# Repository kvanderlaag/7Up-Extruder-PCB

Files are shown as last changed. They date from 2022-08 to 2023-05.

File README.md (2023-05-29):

# 7-Up Amateur Extruder PCB

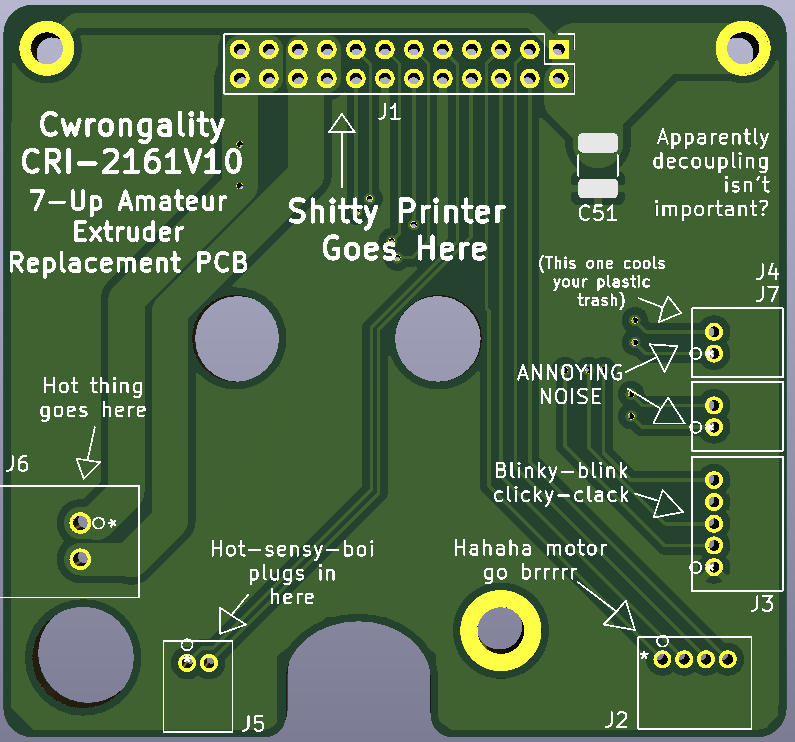
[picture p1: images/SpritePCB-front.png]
Rendering of the front side of a printed circuit board with witty silkscreen text.
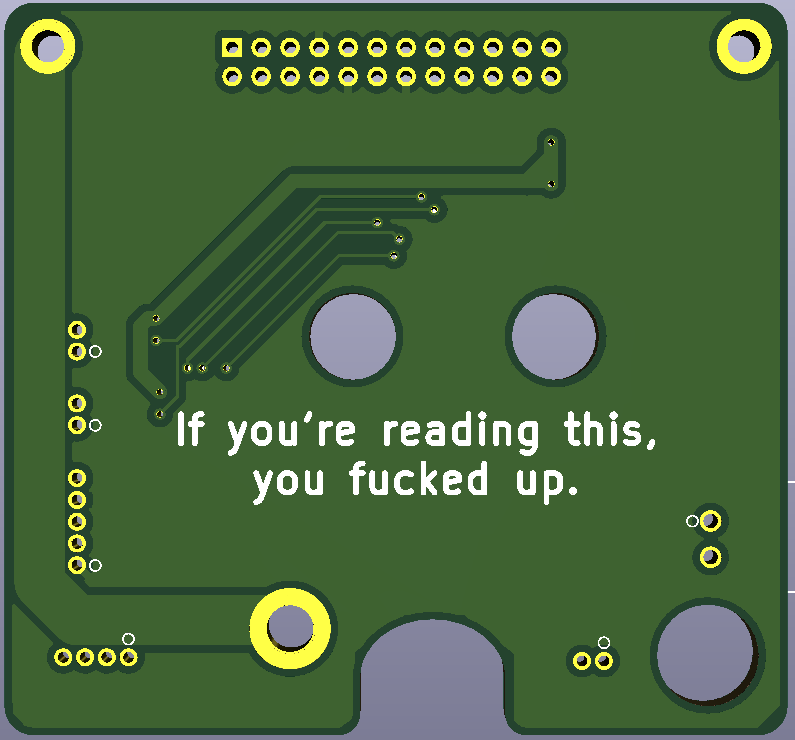
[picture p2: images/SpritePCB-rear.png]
Rendering of the rear side of a printed circuit board with witty silkscreen text.
 

This is a replacement extruder/toolhead PCB for Creality Sprite/Sprite Pro Extruder PCB for Ender-3 series printers -- the Ender-3 S1, Ender-3 S1 Pro, Ender-3 S1 Plus, which all come with a Sprite direct drive extruder out of the box, or an Ender-3, Ender-3 Pro, or Ender-3 V2 that you've retrofitted with the Creality Sprite or Sprite Pro extruder kit.

While fumbling around behind my toolhead with a wrench to adjust the eccentric nut spacer on the X-axis, I managed to ram the wrench into the extruder connector, tearing it off the PCB and taking the solder pads and an appreciable amount of the traces connected to it with it. Naturally, I did this at the worst possible time, when I was printing parts necessary to get my _other_ printer working.

Of note: If you e-mail sales@creality3dofficial.com and request a replacement for this part, they can sell you one! It cost $15 USD shipped. However, while I was waiting to hear back from them, I looked at this PCB and thought, "hell, I could just make one of these."

The connectors on the Creality PCB are: 
- a 2.0mm-pitch, 24-position IDC header, right angle, with locking tabs and eject levers -- they need to be long enough to reach the top of the IDC connector -- for the flat flexible ribbon cable that connects to the printer; ryanpie86 has correctly pointed out that [this connector](https://www.lcsc.com/product-detail/IDC-Connectors_Ckmtw-Shenzhen-Cankemeng-B-3102R24P-A000_C383593.html) on LCSC is a perfect fit, but watch out for LCSC's shipping. It's helpful if you can place an order for a lot of crap together, and you will pay customs fees on it.
- three JST ZH (1.5mm pitch) surface-mount connectors, 2-position, for the thermistor, hotend fan, and part cooling fan
- one JST ZH (1.5mm pitch) surface-mount connector, 4-position, for the extruder motor
- one JST ZH (1.5mm pitch) surface-mount connector, 5-position, for the (optional) CRtouch/BLtouch automatic bed levelling sensor
- one JST XH (2.5mm pitch) through-hole connector, 2-position, for the heater cartridge

I don't know if you've ever soldered these ZH bastards surface-mount before, but they are absolutely hateful little things, and I refuse to do it. ZH is the smallest JST connector size you can get in through-hole flavour, so for this board, I've replaced _all_ of the surface-mount connectors with through-hole variants. I feel like this actually makes this PCB more repairable than the original, and less prone to the thing that destroyed mine in the first place.

The flat flexible cable connector is slightly more problematic. [This](https://www.digikey.ca/en/products/detail/cnc-tech/3110-24-002-13-00/3882488) connector from CnC Tech is exactly what you want -- but it is obsolete and, as far as I can tell, impossible to obtain. Creality are clearly using a connector _like_ this one in the production PCBs, but I haven't been able to find a source for it. If you do, let me know and I'll update the project and this document to point at it. For the time being, I've just carefully desoldered mine from the board and reused it. If you were desperate, you could use a regular shrouded 24-position, 2.0mm pitch, right-angle pin header, but since this part is in motion and dragging the cable around with it, this seems like it probably leads to sadness.

JST connectors are easier to come by, but at the time of this writing (2022-08-25) are spotty at best for stock, with a long lead time. You want the JST [S2B-ZR-3.4(LF)(SN)](https://www.digikey.ca/en/products/detail/jst-sales-america-inc/s2b-zr-3-4-lf-sn/4806278) for the 2-position ZH, [S4B-ZR-3.4(LF)(SN)](https://www.digikey.ca/en/products/detail/jst-sales-america-inc/s4b-zr-3-4-lf-sn/7802286) for the 4-position ZH, [S5B-ZR-3.4(LF)(SN)](https://www.digikey.ca/en/products/detail/jst-sales-america-inc/s5b-zr-3-4-lf-sn/9972250) for the 5-position ZH, and the [S2B-XH-A(LF)(SN)](https://www.digikey.ca/en/products/detail/jst-sales-america-inc/S2B-XH-A-LF-SN/1651055) for the 2-position XH for the heater.

Annoyingly, Chinese replacements available on Alibaba/AliExpress _will_ fit with some massaging, but they are listed at 2.54mm pitch rather than the 2.5mm pitch of "genuine" JSTs. I've designed the board with the JSTs in mind, but there is a distinct probability that the heater cartridge on the Sprite is actually 2.54mm pitch. Again, it should both fit and work whichever one you choose to use, it might just be a little tight on the board if you're using a Chinese XH-style connector, and a little tight fitting the cable into the connector if you're using a genuine JST. The worst of both worlds, really.

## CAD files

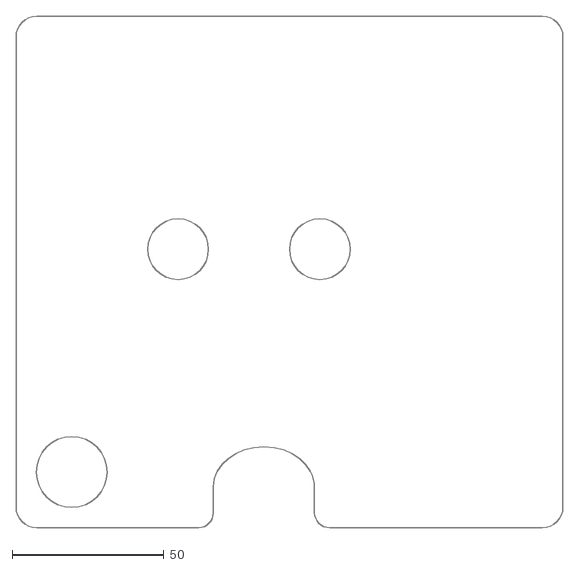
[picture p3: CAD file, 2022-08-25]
Sprite.dxf
180.0 x 168.3

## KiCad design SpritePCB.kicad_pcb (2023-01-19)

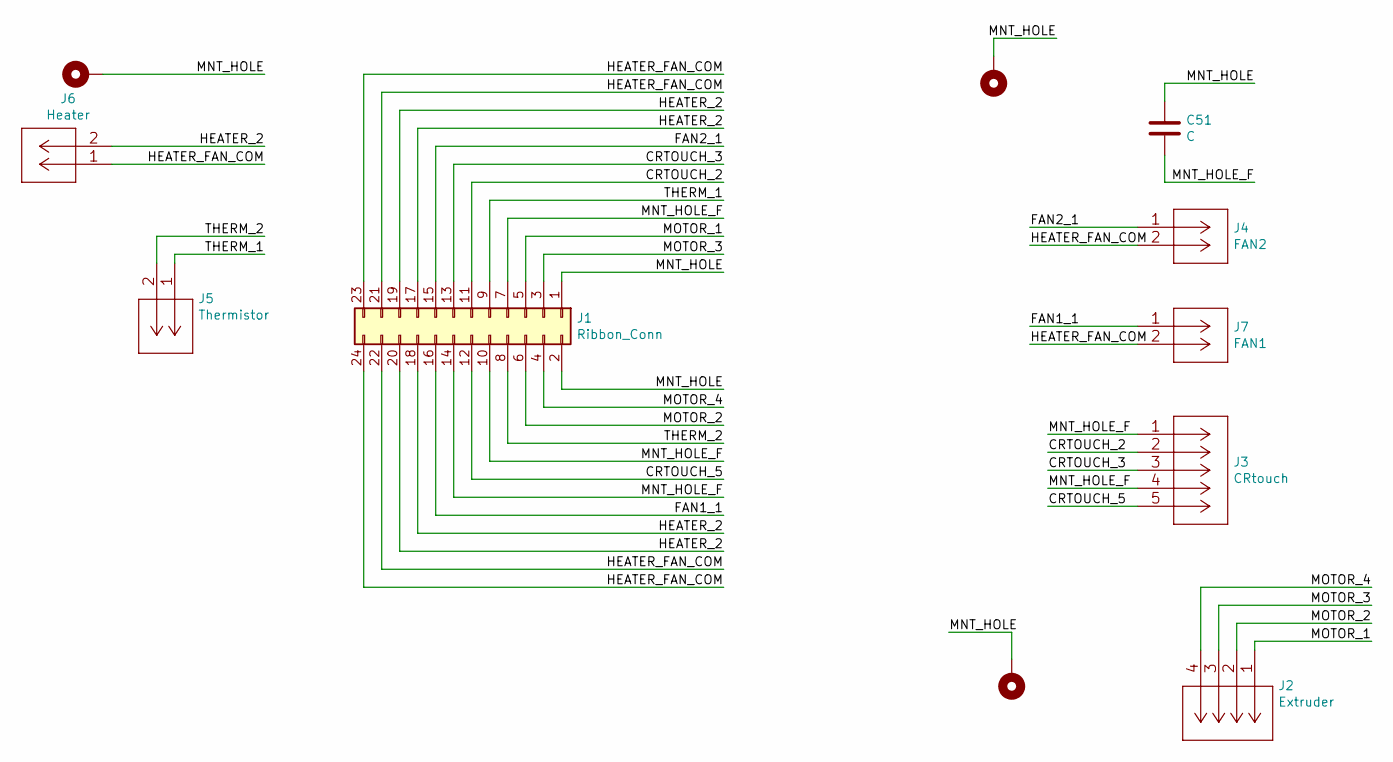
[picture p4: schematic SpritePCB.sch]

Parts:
C51: C; C_1210_3225Metric_Pad1.33x2.70mm_HandSolder
H1, H2: MountingHole_Pad; MountingHole_2.2mm_M2_DIN965_Pad
H3: MountingHole_Pad; MountingHole_3.2mm_M3_DIN965_Pad
J1: Ribbon_Conn; PinHeader_2x12_P2.00mm_Vertical
J2: Extruder; S4B-ZRLFSN
J3: CRtouch; S5B-ZRLFSN
J4: FAN2; S2B-ZRLFSN
J5: Thermistor; S2B-ZRLFSN
J6: Heater; S2B-XH-A-1LFSN
J7: FAN1; S2B-ZRLFSN

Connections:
/CRTOUCH_2: J1.11, J3.2
/CRTOUCH_3: J1.13, J3.3
/CRTOUCH_5: J1.12, J3.5
/FAN1_1: J1.16, J7.1
/FAN2_1: J1.15, J4.1
/HEATER_2: J1.17, J1.18, J1.19, J1.20, J6.2
/HEATER_FAN_COM: J1.21, J1.22, J1.23, J1.24, J4.2, J6.1, J7.2
/MNT_HOLE: C51.1, H1.1, H2.1, H3.1, J1.1, J1.2
/MNT_HOLE_F: C51.2, J1.7, J1.10, J1.14, J3.1, J3.4
/MOTOR_1: J1.5, J2.1
/MOTOR_2: J1.6, J2.2
/MOTOR_3: J1.3, J2.3
/MOTOR_4: J1.4, J2.4
/THERM_1: J1.9, J5.1
/THERM_2: J1.8, J5.2

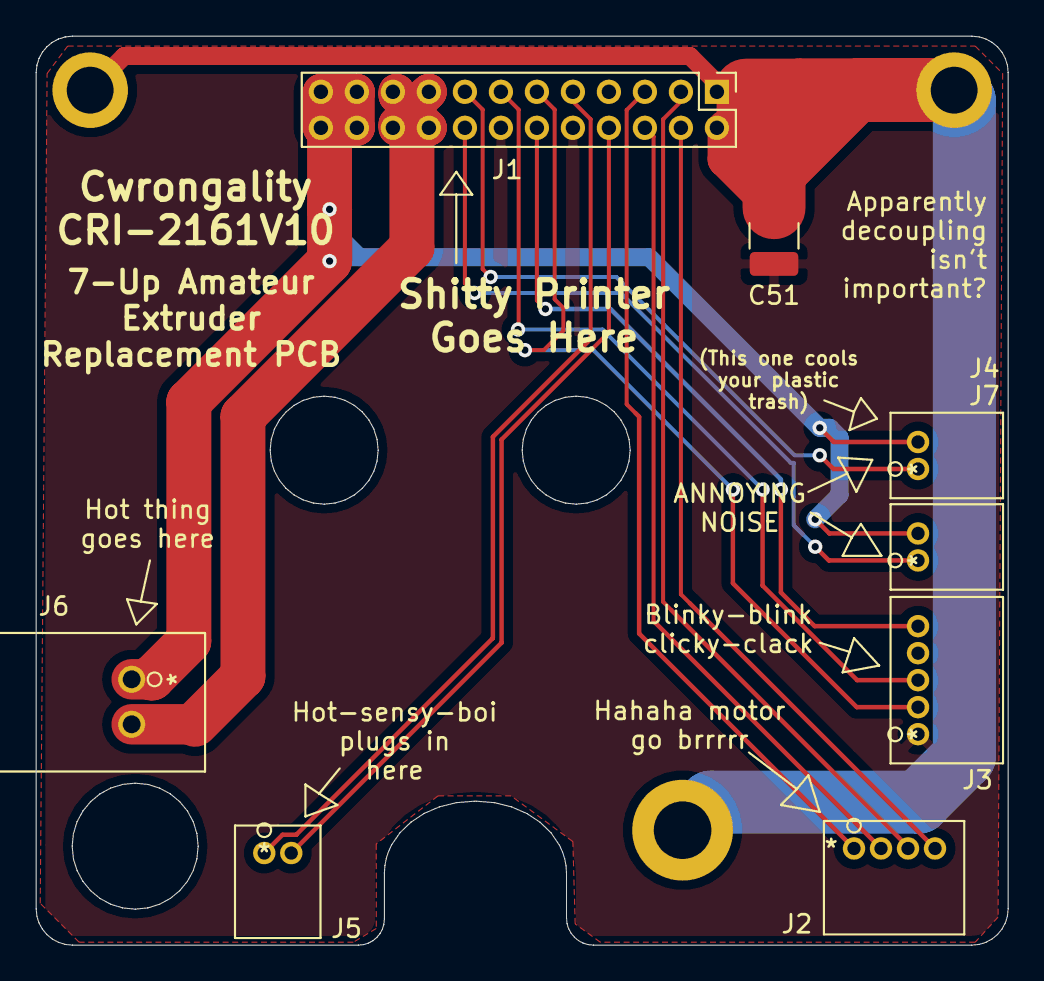
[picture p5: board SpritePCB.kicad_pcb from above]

Board: 2 copper layers, 54.0 x 50.5 mm, 11 parts (0 on the bottom side), 15 nets.

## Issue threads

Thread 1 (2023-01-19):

overlapping tracks/signals intruduced in commit 18d3b11

Darthyson, 2023-01-19:
commit 18d3b11 made the PCB useless by overlapping nearly all tracks/signals.

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

kvanderlaag, 2023-01-19:
Fixed in https://github.com/kvanderlaag/7Up-Extruder-PCB/commit/35ca0986024968bb7b7bcef41f84c75d00d74ad1 -- moving the connector obviously would have misaligned the existing traces, and since they were sandwiched between pins already, naturally they overlapped.

While this is obviously a silly thing to have missed, I feel like it may benefit you to be slightly more tactful in your phrasing when submitting an issue with a screenshot of the board editor when the fix takes about as long as writing "Commit 18d3b11 made the PCB useless."

Darthyson, 2023-01-19:
I'm sorry I did not mean to offend you. English is not my first language. Maybe it's an easy fix for you. In eagle i could fix that. KiCad right now i can only use as a viewer. Thanks a lot for your fast response and fix.

Closed 2023-01-19.

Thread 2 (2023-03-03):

common 24v pin?

psi-4ward, 2023-03-03:
Hi,
I read about a 24V common PIN - do you know if I can catch 24V to power a LED?
Thx

kvanderlaag, 2023-05-29:
The heater and fans all share a common power line -- _I believe_ -- on pins 21-24 of the 24-pin connector. (I'm trusting that this thing is designed by a sane human being and they share power and switch on ground, I don't actually own one to check it anymore.) You should be able to solder to any of those four pads to get 24V if you need it, and the common ground pins are 1 and 2 way over on the other side. It would be a relatively trivial add to throw either another two-pin connector on the board for auxiliary power, or a couple of test points to solder to, but I can't remember offhand where it would be safe to put those for mechanical clearance.

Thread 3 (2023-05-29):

IDC connector - I think I found it

ryanpie86, 2023-05-29:
https://www.lcsc.com/product-detail/IDC-Connectors_Ckmtw-Shenzhen-Cankemeng-B-3102R24P-A000_C383593.html

kvanderlaag, 2023-05-29:
That's the one! Thank you, I should have thought to check LCSC for this, I'll add it to the BOM.

Closed 2023-05-29.

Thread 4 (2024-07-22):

It looks like cr-touch is not connected properly

kriku, 2024-07-22:
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

kriku, 2024-07-22:
4 pin is floating

kriku, 2024-07-22:
and looks like you don't use all of common ground cables

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

all goes through pin 7 of sprite cable

VoxelTek, 2024-08-31:
From what I can tell, pin 4 isn't even connected on the original official board. Mine doesn't seem to connect to any traces. I don't know enough about the BL/CR touch, but maybe the pin just...isn't necessary for normal functionality?

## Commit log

2022-08-25 Initialize repository with project files
    [Sprite.dxf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]
2022-09-04 Corrected misaligned drills
    Corrected misaligned motor mount hole (originally slightly too high and too far left); shifted FFC connector left slightly to align better with the cable bracket; widened cutout for POM adjuster slightly on the left; enlarged M2 mounting holes for cable bracket slightly.
    After receiving the first batch of boards, I noticed that I'd done math wrong on the motor mounting hole positions. (Did the math based on the edge, not the centre, because I'm stupid. I also made some slight tweaks to other items to get it to line up a little better with the original board's cutouts, but all in, it was actually pretty close!
    One thing to note: The connectors that were prev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
    [SpritePCB.kicad_pcb]
2023-01-19 Fix issue #1: overlapping tracks/signals introduced in commit 18d3b11
    Moving the dual-row header in commit 18d3b1 resulted in misaligned traces overlapping with the new hole positions. Don't commit changes while tired, folks.
    [SpritePCB-B_Adhes.gbr, SpritePCB-B_Cu.gbr, SpritePCB-B_Mask.gbr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]
2023-05-29 Update BOM with link to 2mm-pitch 24-position IDC connector
